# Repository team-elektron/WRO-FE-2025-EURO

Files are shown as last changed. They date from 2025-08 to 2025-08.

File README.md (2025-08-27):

# Elektron Team - WRO Future Engineers 2025 - Bosnia and Herzegovina

## Content

* `t-photos` contains 2 photos of the team (an official one and one funny photo with all team members)
* `v-photos` contains 6 photos of the vehicle (from every side, from top and bottom)
* `video` contains the video.md file with the link to a video where driving demonstration exists
* `schemes` contains schematic diagrams of the driving base.
* `src` contains code of control software for all components which were programmed to participate in the competition.
* `models` is for the files for models used by 3D printers to produce the vehicle elements.
* `other` is for other files which can be used to understand how to prepare the vehicle for the competition.

## Introduction

This is the public repository for our team and the work we have done on our robot.

<p float="left">
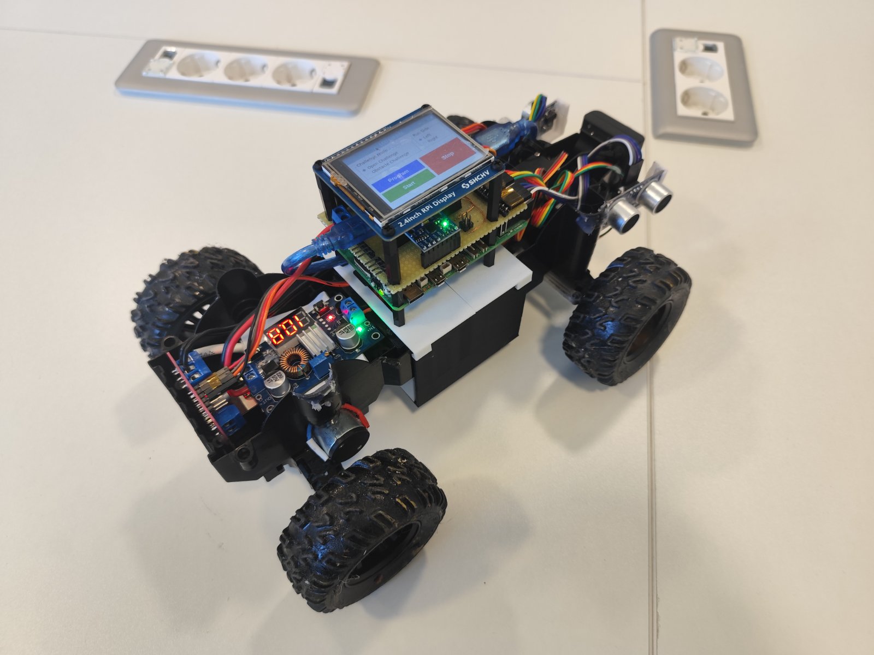
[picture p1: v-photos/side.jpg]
  
  &nbsp;
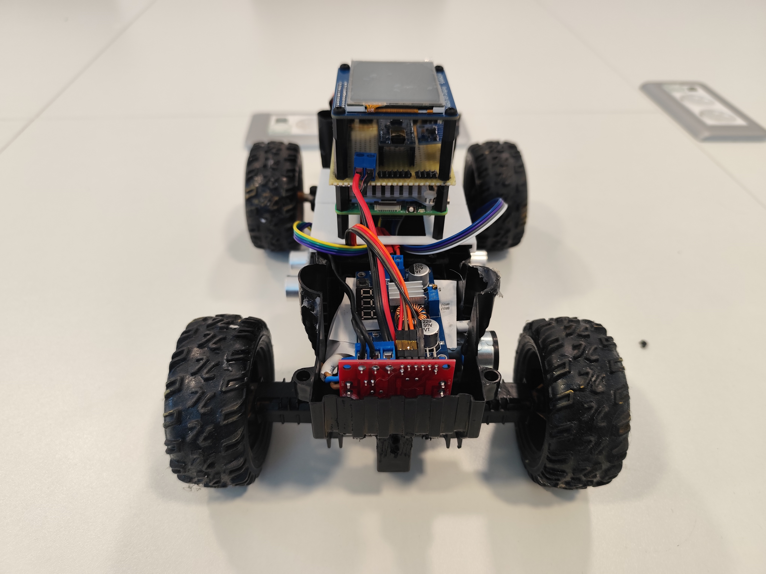
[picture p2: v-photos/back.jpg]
  
</p>

## Design elements

### Technical specifications
- Power: 3s1p Li-Ion Battery (EVE ICR18650-26v)
- Control: Raspberry Pi 5 8GB SBC
- Movement: Brushed motor
- Steering: 180 degree Servo based
- Sensors: 3x Ultrasonic sensors, Camera, IMU Sensor
- Displays: 2.4 Inch LCD Touch Display

### Driving elements

For the driving base we have chosen a pre-made RC car driving base due to time constraints. The main driving motor is controled by a L298N Motor H-Bridge controller and a 180 degree servo for steering. 

<p float="left">
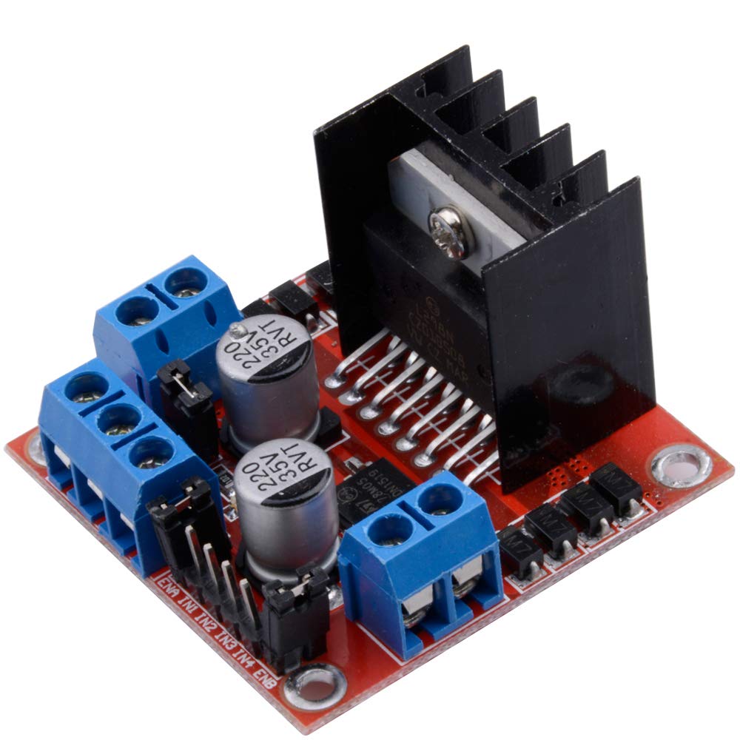
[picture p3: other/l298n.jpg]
  
  &nbsp;
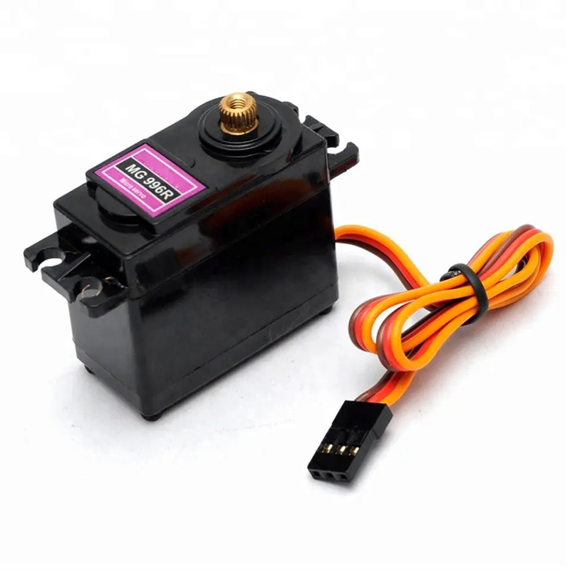
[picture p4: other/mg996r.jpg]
  
  &nbsp;
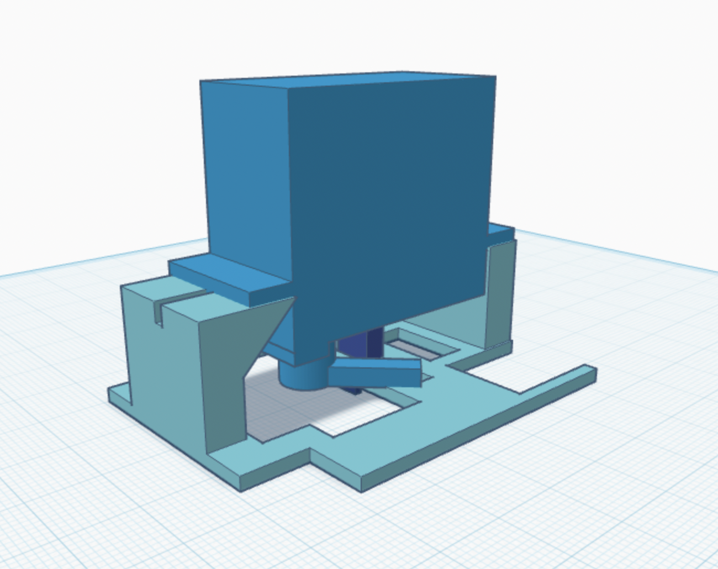
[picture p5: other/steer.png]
  
</p>

### Cameras & Sensors

On our robot we have utilised a MPU-6050 IMU sensor for detecting the rotation angle when steering. 
The "eyes" of the operation are a set of 3 HC-SR04 Ultrasonic sensors and a standard USB Webcam.

<p float="left">
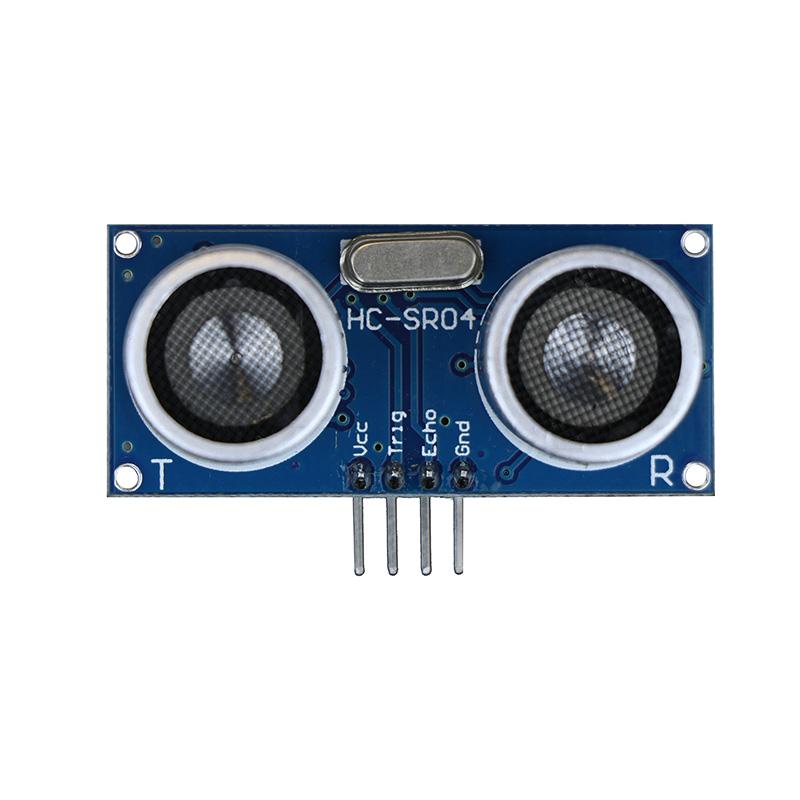
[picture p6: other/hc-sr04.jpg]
  
  &nbsp;
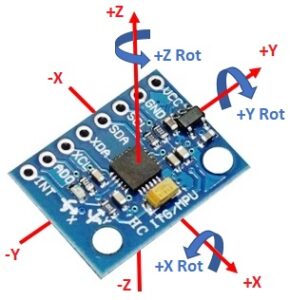
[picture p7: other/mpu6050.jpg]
  
  &nbsp;
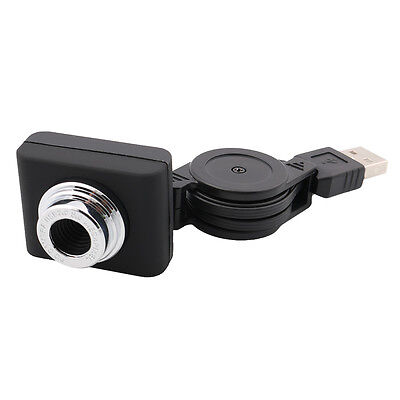
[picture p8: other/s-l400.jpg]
  
</p>

### Power supply and control elements

For the power supply we chose a custom made 18650 based battery in the 3s1p configuration which can be quickly charged with USB-C at 3A continuous. 
This gives us around 27.5Wh (2.55Ah @ 10.8v nominal) to work with which is plenty for the job at hand.

<p float="left">
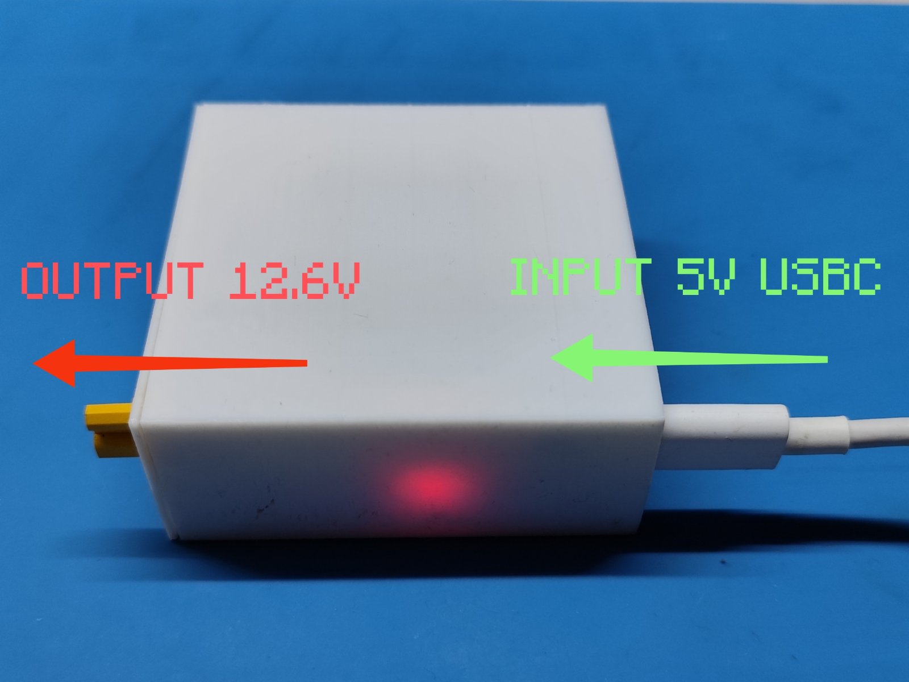
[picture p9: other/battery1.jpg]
  
  &nbsp;
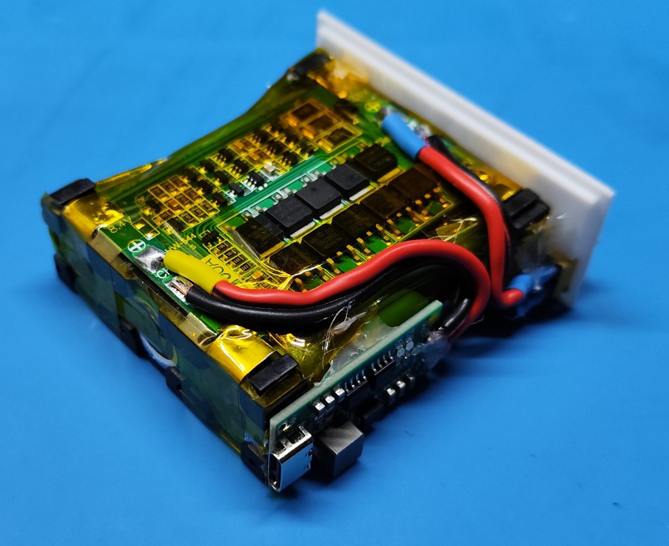
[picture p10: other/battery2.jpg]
  
</p>

The robot is based on a Raspberry Pi 5 which requires a stable power input of 5v @ 5A, for this job we have first chosen an UBEC voltage regulator, but due to the specific adapter we got not actually being able to handle the Pi, we had to switch to a more readily available replacement, the XL4015.

<p float="left">
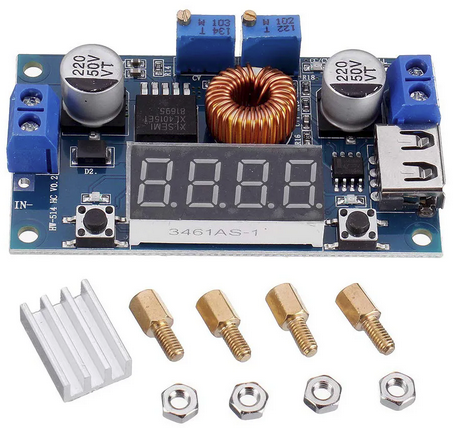
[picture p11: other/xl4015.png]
  
  &nbsp;
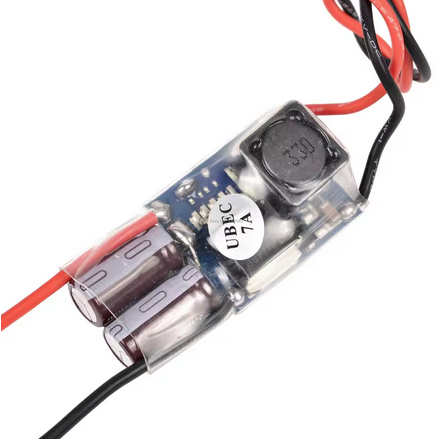
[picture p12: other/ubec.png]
  
</p>

We have designed a custom Pi GPIO shield to more easily wire up all of our power sources and sensors. The design for this PCB can be found in the schemes folder.

<p float="left">
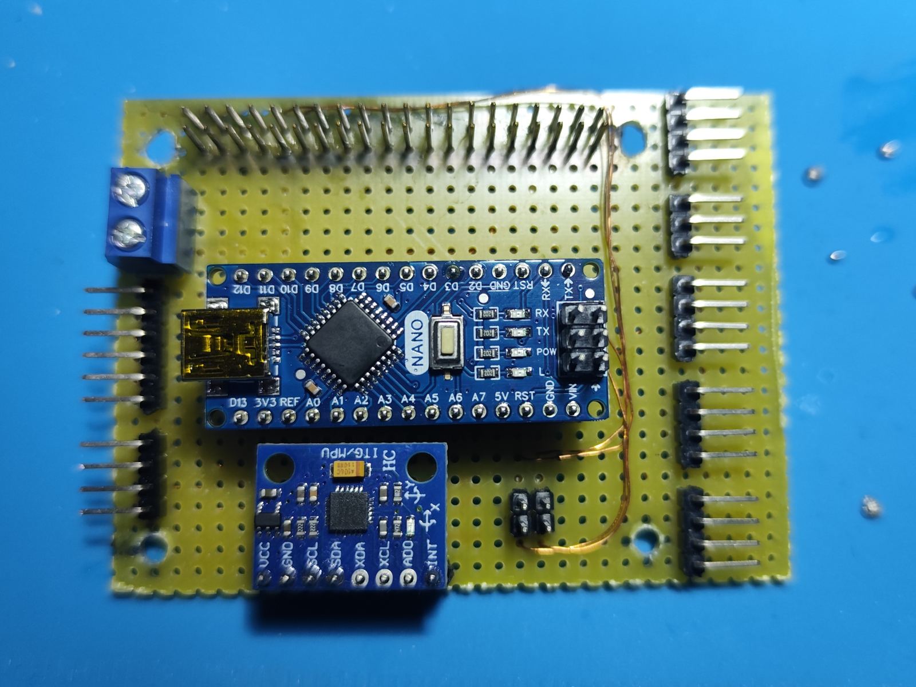
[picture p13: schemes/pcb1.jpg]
  
  &nbsp;
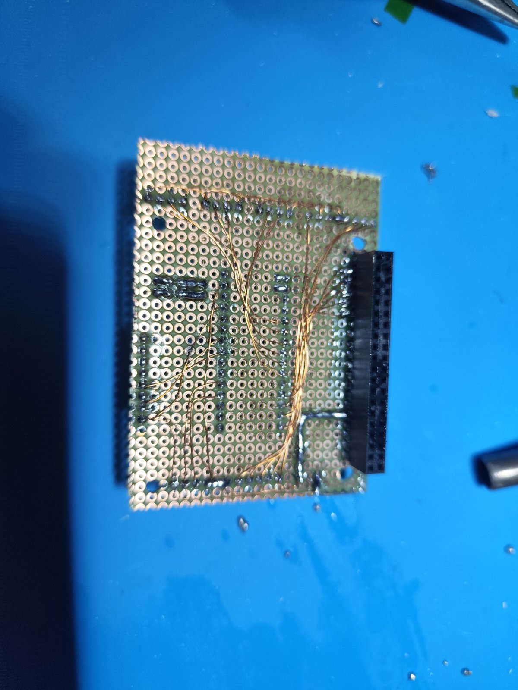
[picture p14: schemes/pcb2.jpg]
  
  &nbsp;
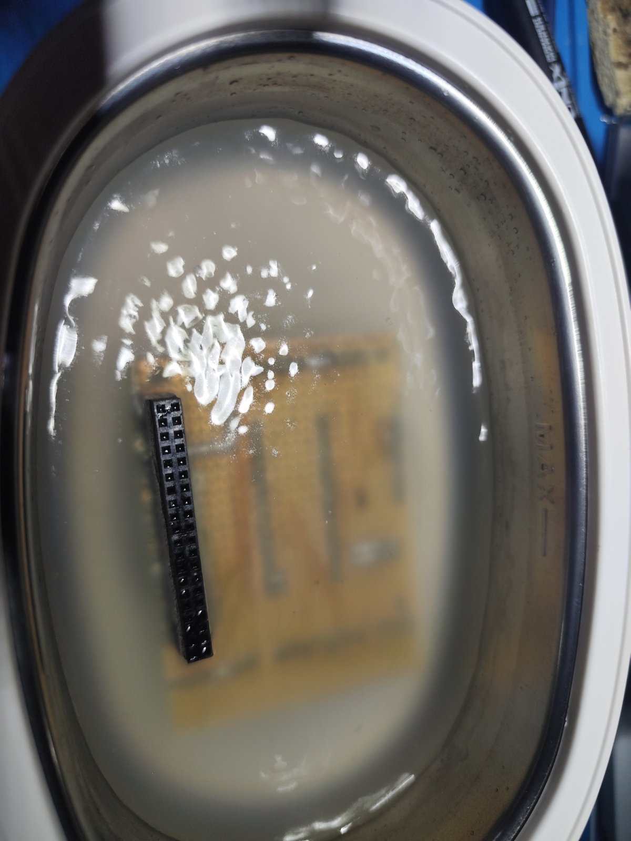
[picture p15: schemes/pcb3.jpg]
  
</p>

On this specific shield you can find an Arduino nano which is used to control all of the sensor inputs and motor outputs. This takes load off of the Raspberry Pi and allows for easier coding. The Arduino communicates to the Pi using a direct UART interface between the two which allows the Nano to handle the "Open Challange" all by itself reducing overall battery consumption (unlike our previous design where the Pi controlled everything).

The shield itself is a major improvement to the earlier revision as it no longer relies on a 20cm long gpio extension wire to the Pi which caused us major issues with powering the Pi because of low quality copper .

### Code

We have written most of our code in Python (mainly OpenCV for obstacle detection) and Arduino flavored c++. 
You can find the code in the src folder and the instructions on how to use it.

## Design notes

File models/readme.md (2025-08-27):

# 3D Printed files

These are the 3d print files we used to convert our rc chassis to a more precise robot chassis.

### 3D printer configuration:

Printer specs:
- Model: Creality Ender 3 V3 KE
- Slicer: OrcaSlicer (Klipper)
- Material: CopyMaster3D PETG White
- Infill: 15% on non structural or moving parts, at least 50% on structural and moving parts
- Print resolution: 0.24mm for larger parts, 0.16mm for gears and fine parts

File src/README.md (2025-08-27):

Control software
====

Since our robot is divided into 2 sections, the Raspberry Pi and the Arduino Nano, we have separated their source files into 2 directories. 

"pi-side" - Raspberry Pi source side,
"nano-side" - Arduino Nano side

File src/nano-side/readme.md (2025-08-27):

Dependencies for the Arduino Nano side of the robot:
- HCSR04 Library by "gamegine", version 2.0.3
- MPU6050 Library by "Adafruit", version 2.2.6
- SoftPWM Library by "Brett Hagman", version 1.0.1

All of these libraries can be found in the library manager in Arduino IDE.
Other core dependencies can be found in the code.

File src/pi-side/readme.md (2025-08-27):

Dependencies for the Raspberry Pi side of the robot:

    AVRDUDE
    Python 3.x (Tkinter, Serial)
    Raspberry Pi OS Bookworm (Debian 12)

"run.sh" is used for starting the main GUI interface from the desktop and killing the start menu process to conserve screen space. The file "./robot/main.py" handles the main gui interface for the robot, obstacle mode selection and programming of the Arduino Nano through avrdude. Compiled HEX files for AVRDUDE are located in the "./robot/arduhex" folder.

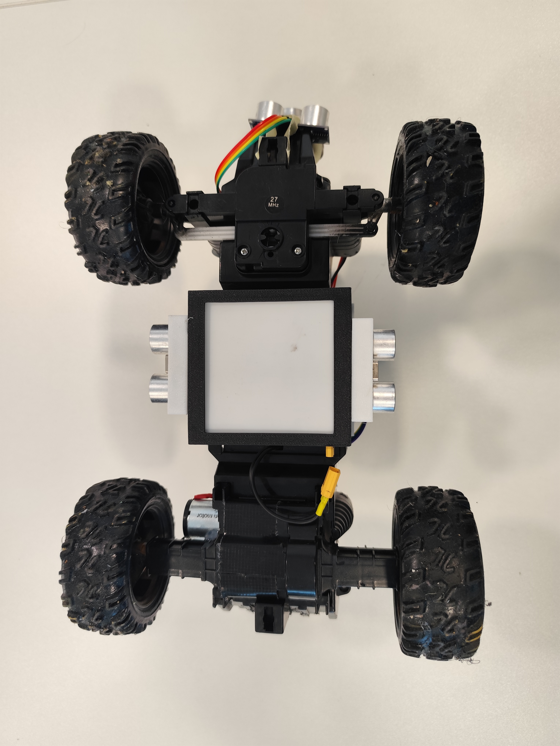
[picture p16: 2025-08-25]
v-photos/bottom.jpg

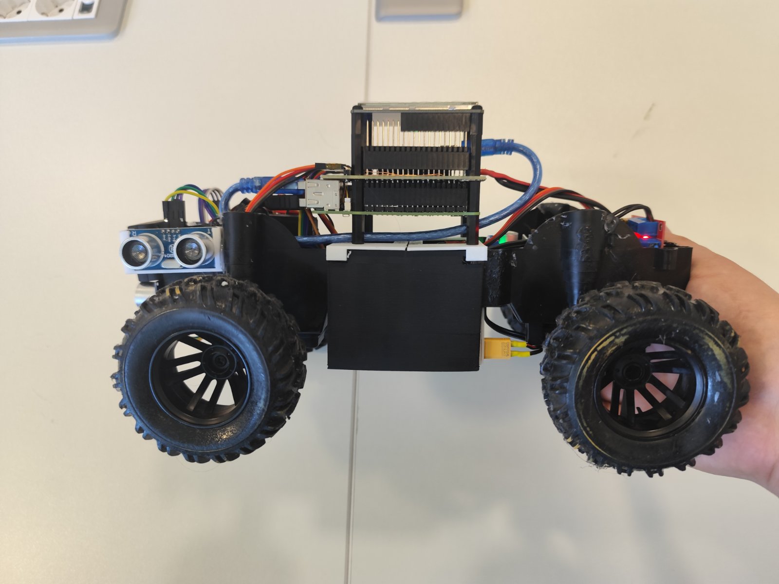
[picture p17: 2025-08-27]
v-photos/left.jpg

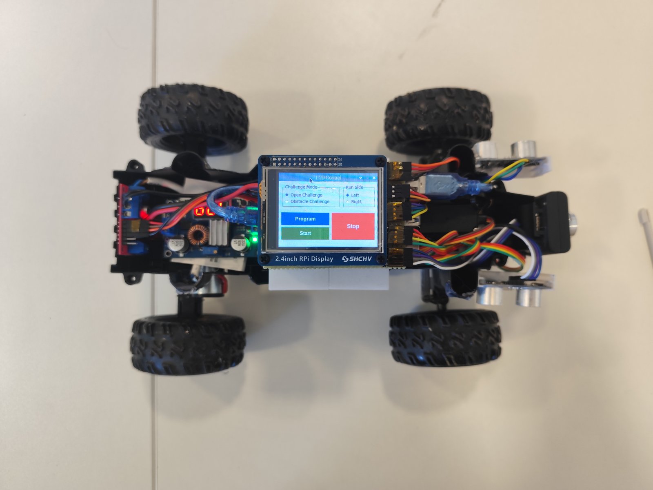
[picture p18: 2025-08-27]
v-photos/top.jpg

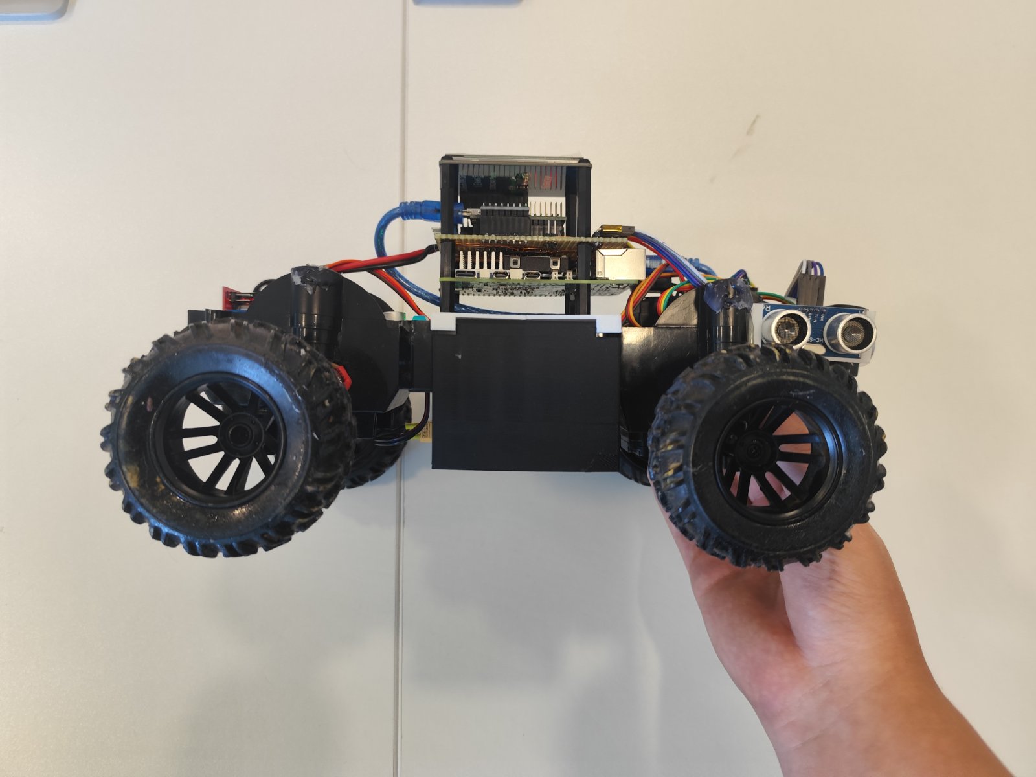
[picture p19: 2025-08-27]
v-photos/right.jpg

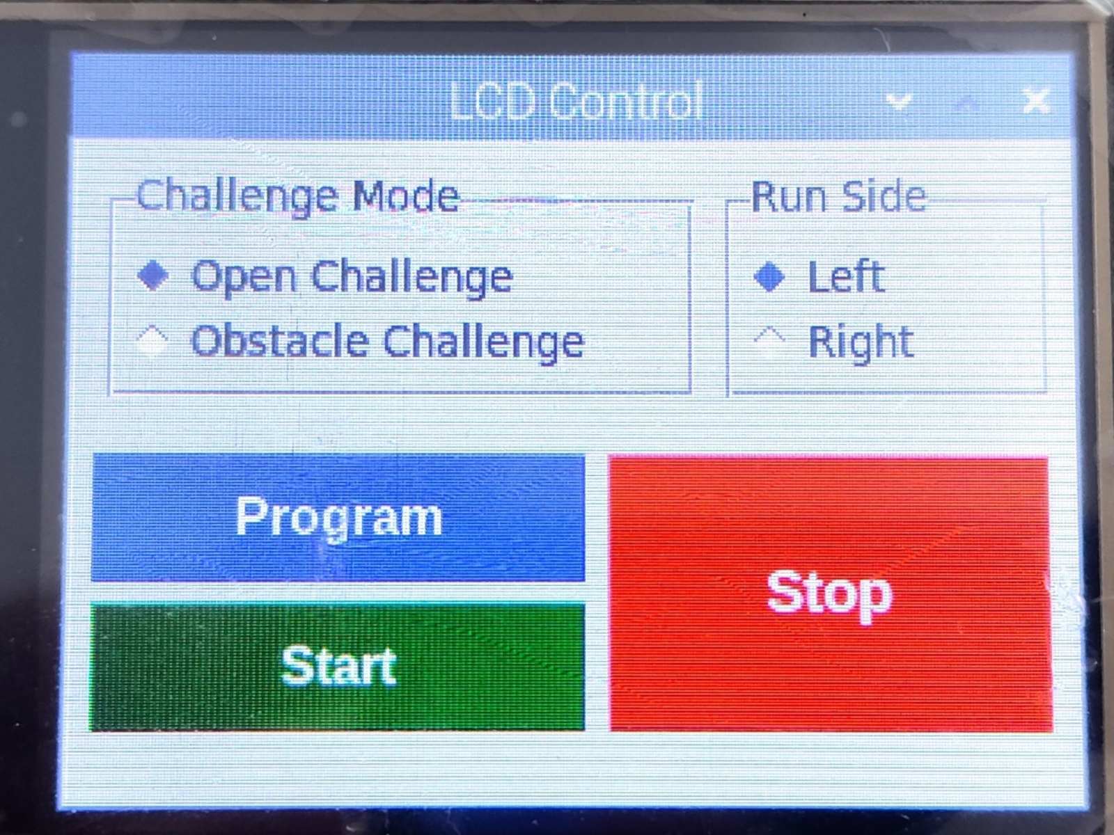
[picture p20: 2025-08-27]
other/gui.jpg

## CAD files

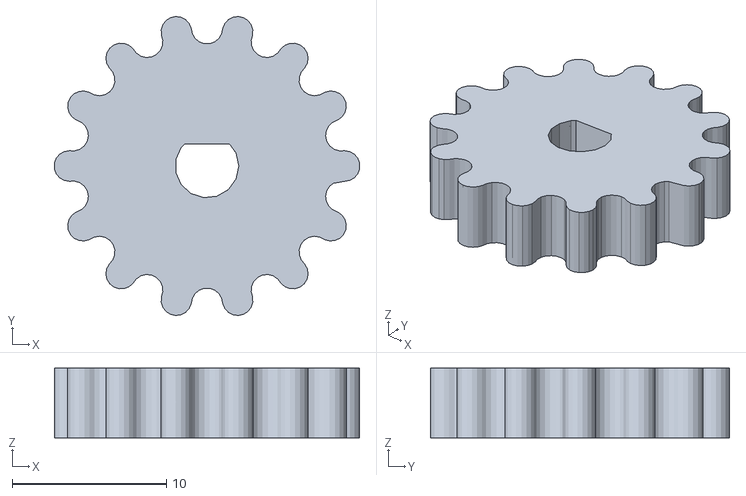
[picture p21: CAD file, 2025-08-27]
models/motor gear.stl
19.8 x 19.4 x 4.50

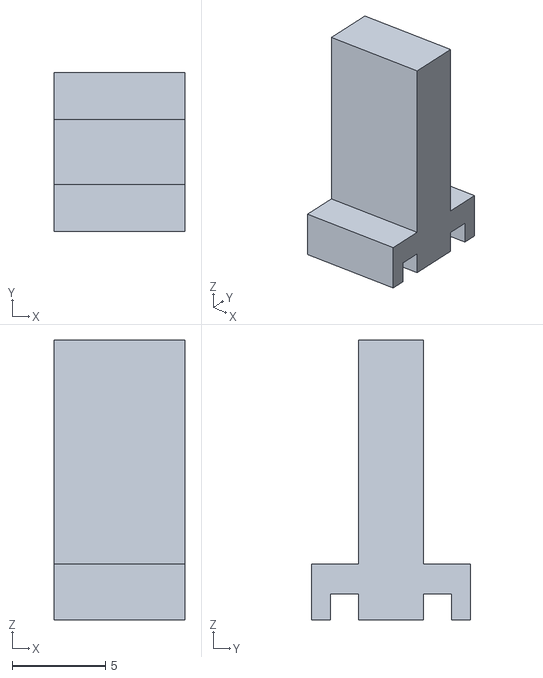
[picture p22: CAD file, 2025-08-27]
models/steering rod.stl
7.00 x 8.50 x 15.0

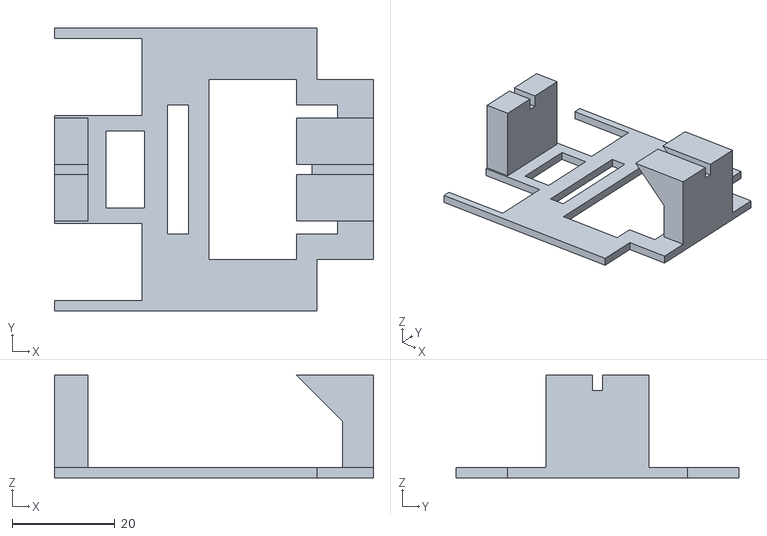
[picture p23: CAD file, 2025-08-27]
models/steering mounts.stl
62.0 x 55.0 x 20.0

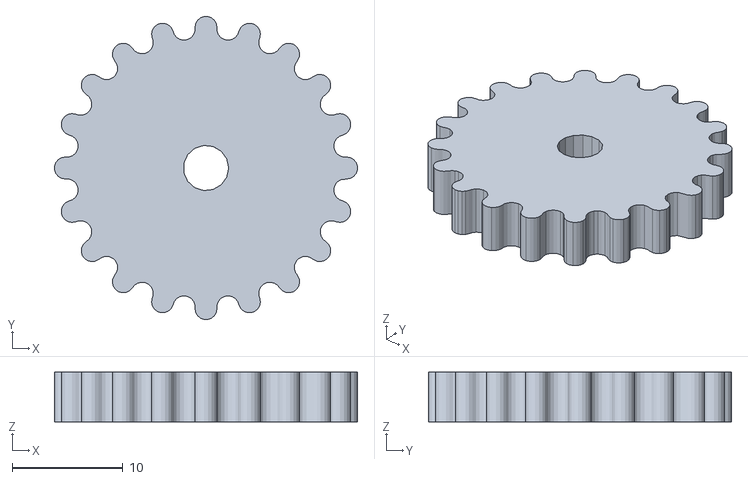
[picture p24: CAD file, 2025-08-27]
models/wheel gear.stl
27.4 x 27.4 x 4.50

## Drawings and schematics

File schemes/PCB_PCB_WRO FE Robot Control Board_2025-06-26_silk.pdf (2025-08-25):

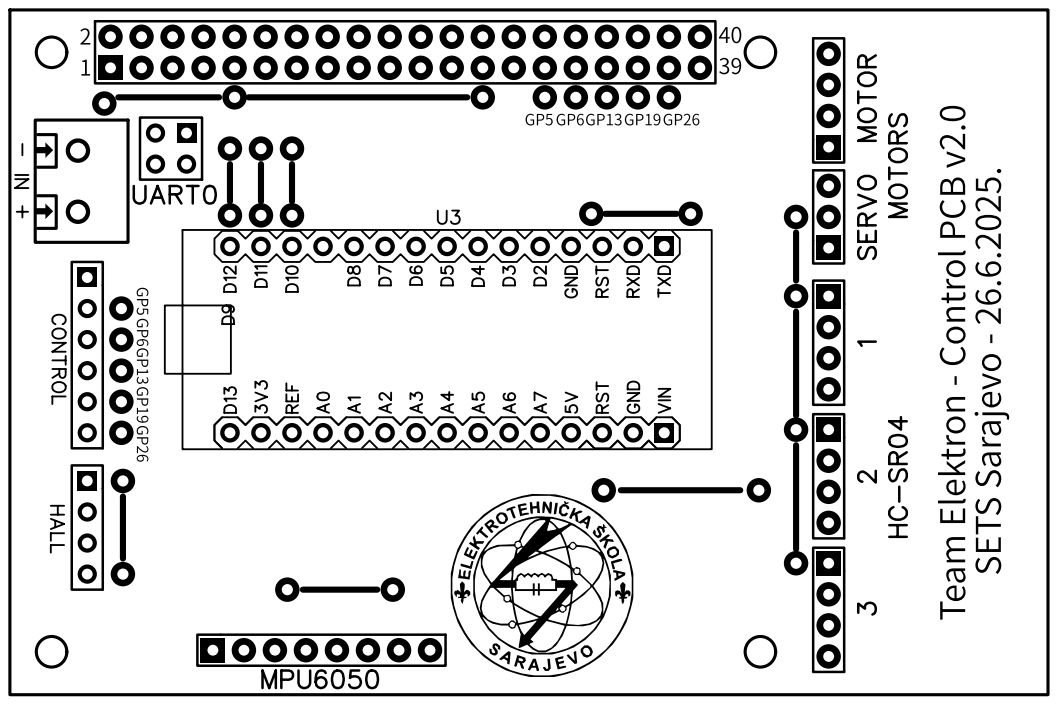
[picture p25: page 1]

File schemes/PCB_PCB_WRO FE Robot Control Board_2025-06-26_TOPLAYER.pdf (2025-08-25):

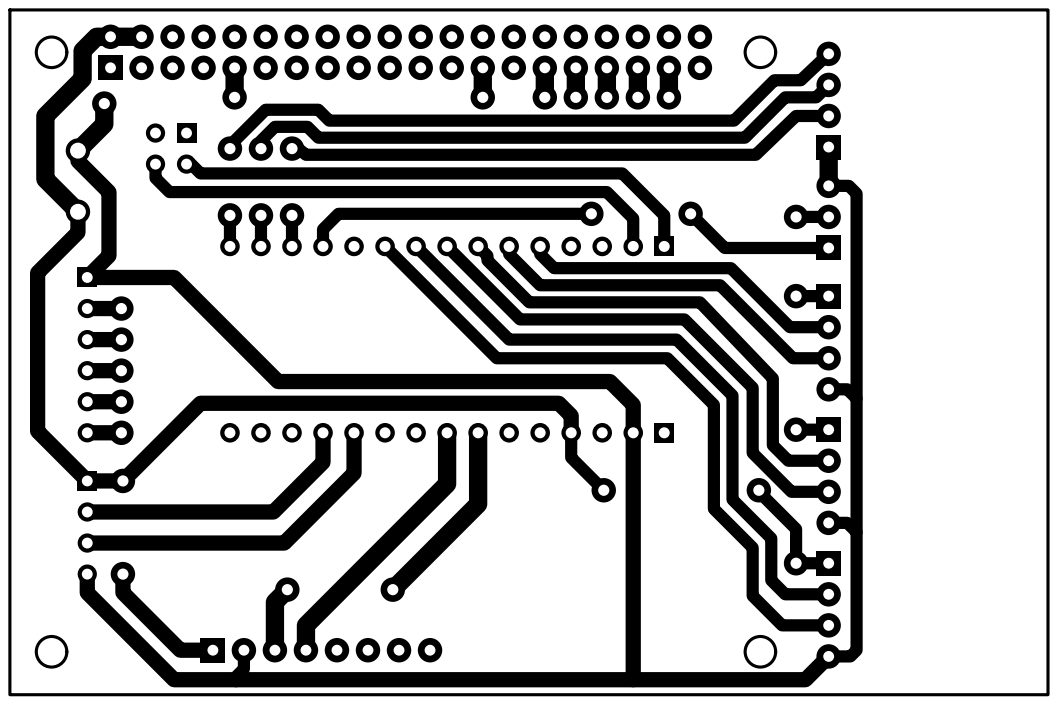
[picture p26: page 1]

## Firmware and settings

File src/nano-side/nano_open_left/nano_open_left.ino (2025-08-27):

//#include <SoftPWM_timer.h>
#include <SoftPWM.h>
#include <Wire.h>
#include <Adafruit_MPU6050.h>
#include <Adafruit_Sensor.h>
#include <HCSR04.h>
#include <Servo.h>

Servo steering;
const int servoPin = 9;

// calibration
const int centerPos = 90;
const int leftPos   = 50;
const int rightPos  = 130;

int gomode = 0;
int str = 0;

HCSR04 left(2, 3);
HCSR04 front(4, 5);
HCSR04 right(6, 7);

Adafruit_MPU6050 mpu;

// Global variables
float yaw = 0.0;          // current yaw angle (degrees)
unsigned long lastTime;   // for delta time

int mot_ena = 11; //Motor Enable/Speed
int mot_in1 = 10; //Motor IN1
int mot_in2 = 12; //Motor IN2

void setup() {
  Serial.begin(115200);

  // Initialize
  //SoftPWMBegin();

  // Create and set pin 13 to 0 (off)
  //SoftPWMSet(10, 0);

  // Set fade time for pin 13 to 100 ms fade-up time, and 500 ms fade-down time
  //SoftPWMSetFadeTime(10, 100, 100);

  steering.attach(servoPin);
  centerSteering();

  if (!mpu.begin()) {
    Serial.println("Failed to find MPU6050 chip");
    while (1) {
      delay(10);
    }
  }
  mpu.setAccelerometerRange(MPU6050_RANGE_8_G);
  mpu.setGyroRange(MPU6050_RANGE_500_DEG);
  mpu.setFilterBandwidth(MPU6050_BAND_21_HZ);
  lastTime = millis();


}

// ---- Update yaw continuously ----
void updateYaw() {
  sensors_event_t a, g, temp;
  mpu.getEvent(&a, &g, &temp);

  // Calculate elapsed time (s)
  unsigned long now = millis();
  float dt = (now - lastTime) / 1000.0;
  lastTime = now;

  // g.gyro.z is in rad/s → convert to deg/s
  float gyroZ = g.gyro.z * 57.2958;

  // integrate yaw
  yaw += gyroZ * dt;

  // keep yaw in range [-180, 180]
  if (yaw > 180) yaw -= 360;
  if (yaw < -180) yaw += 360;
}

// ---- Function you can call anywhere to get yaw ----
float getYaw() {
  updateYaw();
  return yaw;
}

void turnLeft(int percentage) {
  percentage = constrain(percentage, 0, 100);
  int angle = map(percentage, 0, 100, centerPos, leftPos);
  steering.write(angle);
}

void turnRight(int percentage) {
  percentage = constrain(percentage, 0, 100);
  int angle = map(percentage, 0, 100, centerPos, rightPos);
  steering.write(angle);
}

void centerSteering() {
  steering.write(centerPos);
}

void resetYaw() {
  yaw = 0.0;
}

void wallFollow() {
  while (true) {
  if (front.dist() >= 70 || front.dist() == 0) {
    delay(10);
    if (left.dist() >= 25) {
      turnLeft(40);
      delay(50);
      analogWrite(mot_ena, 60);
      digitalWrite(mot_in1, HIGH);   // Start forward
      digitalWrite(mot_in2, LOW); //
    } else {
      turnRight(40);
      delay(50);
      analogWrite(mot_ena, 50);
      digitalWrite(mot_in1, HIGH);   // Start forward
      digitalWrite(mot_in2, LOW); //
    }
  } else {
      centerSteering();
      analogWrite(mot_ena, 60);
      digitalWrite(mot_in1, LOW);   // Stop
      digitalWrite(mot_in2, HIGH); //
      delay(50);
      //SoftPWMSetPercent(mot_ena, 0);    //
      analogWrite(mot_ena, 0);
      digitalWrite(mot_in1, LOW);   // Stop
      digitalWrite(mot_in2, LOW); //
      delay(1000);
      break;
    
  } 
}
}

void rightTurn() {
  while (true) {
    float currentYaw = getYaw();
    delay(50);
    Serial.println(currentYaw);
    if (currentYaw >=-85) {
      turnRight(100);
      analogWrite(mot_ena, 65);
      digitalWrite(mot_in1, HIGH);   // Start forward
      digitalWrite(mot_in2, LOW); //
    } else {
      centerSteering();
      analogWrite(mot_ena, 0);
      digitalWrite(mot_in1, LOW);
      break;
    }
  }
}

void loop() {
  
  float currentYaw = getYaw();
  
  Serial.print("Yaw: ");
  Serial.println(currentYaw);
  Serial.print("Ultrasonic left: ");
  Serial.println(left.dist());
  delay(60);
  Serial.print("Ultrasonic righ: ");
  Serial.println(right.dist());
  delay(60);
  Serial.print("Ultrasonic front: ");
  Serial.println(front.dist());
  delay(60);

  if (Serial.available()) {
    char c = Serial.read();
    if (c == 'r') {
      yaw = 0;
      Serial.println("Yaw reset!");
    }
    if (c == 'o') {
      for (int i = 0; i < 12; i++) {
        wallFollow();
        delay(1000);
        resetYaw();
        rightTurn();
      }
    }
  }



}

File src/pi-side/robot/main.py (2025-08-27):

import tkinter as tk
from tkinter import ttk
import subprocess
import threading

root = tk.Tk()
root.title("LCD Control")
root.geometry("320x212+0+28")  # account for top bar
root.resizable(False, False)

# === Variables for radio button groups ===
challenge_mode = tk.StringVar(value="Open Challenge")
run_side = tk.StringVar(value="Left")

# === Top row: radio buttons inline ===
radio_frame = ttk.Frame(root, padding=5)
radio_frame.pack(fill="x", pady=5)

# Challenge Mode (left)
challenge_frame = ttk.LabelFrame(radio_frame, text="Challenge Mode", padding=5)
challenge_frame.pack(side="left", expand=True, fill="both", padx=5)

ttk.Radiobutton(challenge_frame, text="Open Challenge", variable=challenge_mode, value="Open Challenge").pack(anchor="w")
ttk.Radiobutton(challenge_frame, text="Obstacle Challenge", variable=challenge_mode, value="Obstacle Challenge").pack(anchor="w")

# Run Side (right)
run_frame = ttk.LabelFrame(radio_frame, text="Run Side", padding=5)
run_frame.pack(side="right", expand=True, fill="both", padx=5)

ttk.Radiobutton(run_frame, text="Left", variable=run_side, value="Left").pack(anchor="w")
ttk.Radiobutton(run_frame, text="Right", variable=run_side, value="Right").pack(anchor="w")

# === Button actions ===
def run_program_command():
    cm = challenge_mode.get()
    side = run_side.get()
    print(f"Program pressed -> Challenge: {cm}, Side: {side}")

    # Run different avrdude commands depending on combo
    if cm == "Open Challenge" and side == "Left":
        subprocess.run([
            "avrdude", "-v",
            "-patmega328p",
            "-carduino",
            "-P/dev/ttyUSB0",
            "-b115200",
            "-D",
            "-Uflash:w:/home/ngx/Desktop/robot/arduhex/nano_open_left.hex"
        ])
    elif cm == "Open Challenge" and side == "Right":
        subprocess.run([
            "avrdude", "-v",
            "-patmega328p",
            "-carduino",
            "-P/dev/ttyUSB0",
            "-b115200",
            "-D",
            "-Uflash:w:/home/ngx/Desktop/robot/arduhex/nano_open_right.hex"
        ])
    elif cm == "Obstacle Challenge" and side == "Left":
        subprocess.run([
            "avrdude", "-v",
            "-patmega328p",
            "-carduino",
            "-P/dev/ttyUSB0",
            "-b115200",
            "-D",
            "-Uflash:w:/home/ngx/Desktop/robot/arduhex/nano_obstacle_left.hex"
        ])
    elif cm == "Obstacle Challenge" and side == "Right":
        subprocess.run([
            "avrdude", "-v",
            "-patmega328p",
            "-carduino",
            "-P/dev/ttyUSB0",
            "-b115200",
            "-D",
            "-Uflash:w:/home/ngx/Desktop/robot/arduhex/nano_obstacle_right.hex"
        ])

# Program button wrapper for threading
def program_action():
    threading.Thread(target=run_program_command).start()

def start_action():
    cm = challenge_mode.get()
    print(f"Start pressed -> Challenge: {cm}")

    if cm == "Open Challenge":
        # Run the Python command in a thread
        def run_start_command():
            import serial
            import time
            # Open the serial port
            ser = serial.Serial("/dev/ttyUSB0", 115200)
            # Wait for Arduino Nano to reset and bootloader to finish
            time.sleep(2)
            # Send the 'o' character
            ser.write(b'o')
            # Close the serial port
            ser.close()

        threading.Thread(target=run_start_command).start()


def stop_action():
    print("Stop pressed")  # placeholder

# === Buttons layout ===
button_frame = ttk.Frame(root, padding=5)
button_frame.pack(fill="both", expand=True)

button_frame.columnconfigure(0, weight=1)
button_frame.columnconfigure(1, weight=1)

# Left column (Program + Start stacked)
program_button = tk.Button(button_frame, text="Program", bg="blue", fg="white",
                           font=("Arial", 12, "bold"), command=program_action)
start_button = tk.Button(button_frame, text="Start", bg="green", fg="white",
                         font=("Arial", 12, "bold"), command=start_action)

program_button.grid(row=0, column=0, sticky="nsew", pady=2, ipadx=5, ipady=5)
start_button.grid(row=1, column=0, sticky="nsew", pady=2, ipadx=5, ipady=5)

# Stop button bigger, to side
stop_button = tk.Button(button_frame, text="Stop", bg="red", fg="white",
                        font=("Arial", 14, "bold"), command=stop_action)
stop_button.grid(row=0, column=1, rowspan=2, sticky="nsew", padx=5, pady=2, ipadx=10, ipady=20)

root.mainloop()
